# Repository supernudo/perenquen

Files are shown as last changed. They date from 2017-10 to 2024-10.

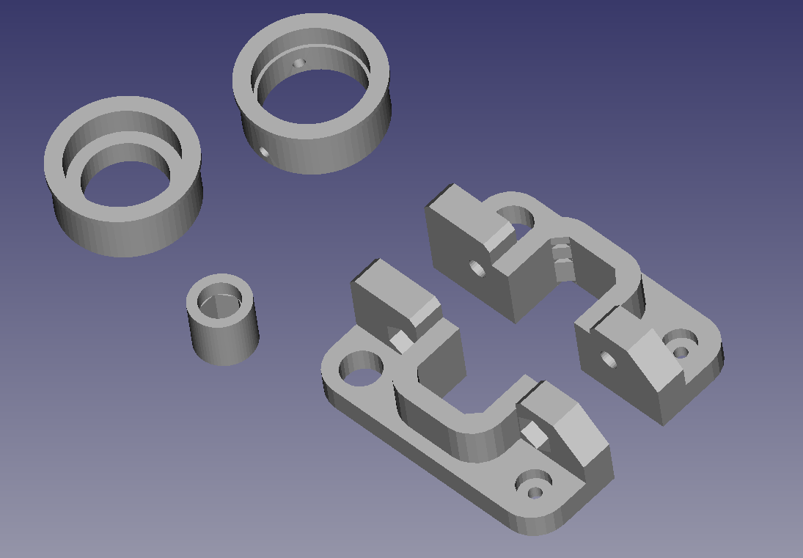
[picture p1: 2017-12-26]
Mechanics/manufacture/Piezas 2017-10-27 18-39-10.png

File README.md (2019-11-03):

# Perenquen

Robot de laberinto o micromouse.

Perenquén es mi primer robot de laberinto. Tiene una tracción diferencial de 4 ruedas diseñada para acelerar en recta a 10m/s/s y alcanza una velocidad de 3m/s. La posición de su centro de masa le permite hacer giros precisos sobre sus ruedas delanteras sin derrapar, a pesar de tener 4 ruedas. Para controlar su velocidad y posición utiliza encoders magnéticos. Durante las curvas utiliza un giroscopo para girar con precisión, independientemente de si derrapan las ruedas. Además, utiliza 4 sensores infrarrojos (2 delanteros y 2 diagonales) para navegar por el laberinto.

## Autor

Javier Baliñas Santos

## Licencia

Todos estos productos están liberados mediante [Creative Commons Attribution-ShareAlike 4.0 International License](http://creativecommons.org/licenses/by-sa/4.0/).  
*All these products are released under [Creative Commons Attribution-ShareAlike 4.0 International License](http://creativecommons.org/licenses/by-sa/4.0/).*

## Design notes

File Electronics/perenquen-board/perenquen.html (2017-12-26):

# Perenquen BOM Rev

Date

Company

# Balitronics

Comment 1

Comment 2

Comment 3

Comment 4

Total Parts

# 97 (Unique 49)

Ref

Qty

Value

Footprint

MPN

[C] -

C2 C9 C8

3

220u 10V

2917(imp) 7343(metric)

T491D227K010AT

C3 C11 C10 C23 C20 C21 C17 C18 C22 C15 C16

11

100n

Capacitors_SMD:C_0603

0603YC104KAT2A

C6

1

10u

Capacitors_SMD:C_0603

T491C106M016AT

C12 C1 C13 C4 C14

5

1u

Capacitors_SMD:C_0603

08053G105ZAT2A

C7

1

10n

Capacitors_SMD:C_0603

06035C103KAT2A

C5

1

470n

Capacitors_SMD:C_0603

0603YD474KAT2A

C19

1

10u 6V LowESR

2312(imp), 6032(metric)

T491C106M016AT

[D] -

D2

1

PWR-ON

0603

SML-D12V1WT86

D6

1

TX-L

LEDs:LED_D5.0mm

SFH4545

D7 D8

2

TX-LD

LEDs:LED_D5.0mm

SFH4545

D9

1

TX-R

LEDs:LED_D5.0mm

SFH4545

D1

1

LED1

0603

SML-D12P8WT86

D3

1

LED2

0603

SML-D12P8WT86

D4

1

LED3

0603

SML-D12P8WT86

D5

1

LED4

0603

SML-D12P8WT86

[J] -

J4

1

MOTOR-R

perenquen motor block

J6 J7

2

ENC-L

perenquen motor block

J1

1

PWR1

B3B-PH-K-S(LF)(SN)

J3

1

MOTOR-L

perenquen motor block

PREC010SAAN-RC

J8 J9

2

ENC-L

pin header 1x4 angled

PREC020SBAN-M71RC

J2

1

ICD

pin header 1x5 angled

PREC020SBAN-M71RC

J5

1

BT

socket strip 1x6 angled

801-87-006-20-001101

[Q] -

Q3

1

RX-L

TEFT4300

Q4

1

RX-R

TEFT4300

Q1 Q2

2

RX-LD

TEFT4300

Q5

1

FLASH

TEFT4300

[R] -

R24 R29 R22 R23 R30

5

1k8 1%

RC0603FR-071K8L

R6 R13 R12

3

0R

RC0805JR-070RL

R5 R8 R4 R7

4

47k

RC0603JR-0747KL

R25 R28

2

12R 1%

RC0805FR-0712RL

R26 R27

2

5.6R 1%

RMCF0805FT5R60

R10 R20

2

10k 1%

RC0603FR-0710KL

R1

1

2R2 1%

RC0603FR-072R2L

R9 R3 R2 R11 R14

5

10k

RC0603FR-0710KL

R15 R17 R18 R21 R16

5

1k

RC0603JR-071KL

R19

1

20k 1%

RC0603FR-0720KL

[SW] -

SW2 SW3 SW4

3

RST

B3U-1000P

SW1

1

450301014042

450301014042

[TP] -

TP1 TP3

2

MagINCn

TP2 TP4

2

MagDECn

[U] -

U2

1

M2940IMPX-5.0/NOPB

TO_SOT_Packages_SMD:SOT-223-3_TabPin2

M2940IMPX-5.0/NOPB

U11

1

DSPIC33EP512MC806

Housings_QFP:TQFP-64_10x10mm_Pitch0.5mm

DSPIC33EP512MC806-I/PT

U8 U7

2

ZXMHC3A01T8

Housings_SOIC:Zetex_SM8

ZXMHC3A01T8

U12

1

ULN2003A

ULN2003A

U6 U1

2

MCP1700

TO_SOT_Packages_SMD:SOT-23

MCP1700T-3302E/TT

U9 U10

2

AS5045B

Housings_SSOP:SSOP-16_5.3x6.2mm_Pitch0.65mm

AS5045B

U4 U3

2

TC4427COA

TC4427COA

U5

1

LY3200ALH

LY3200ALHTR

[Y] -

Y1

1

10Mhz

CSTCE10M0G55-R0

# BOM made with KICAD_BOM_WIZARD (https://github.com/HashDefineElectronics/KiCad_BOM_Wizard) (Generated mar 31 oct 2017 20:18:06 CET)

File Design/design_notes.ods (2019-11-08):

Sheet: motores
 |  | Min7 | Micromouse | Micromouse | Minisumo | Units
Maximum acceration and speed
Robot mass | m | 0,09 | 0,12 | 0,08 | 0,5 | kg | 44,5
Friction coheficient | u | 0,7 | 0,7 | 0,7 | 0,7
Gravity acceleration | g | 9,8 | 9,8 | 9,8 | 9,8 | m/s²
Max. Acceleration | a_max = g * k | 7,00 | 7,00 | 7,00 | 7,00 | m/s²
Max. Speed | v_max | 3,5 | 3 | 3 | 3 | m/s
Maximum power requiered
Force | F_max = m * a | 0,63 | 0,84 | 0,56 | 3,50 | N
Power | P_max = F * v | 2,21 | 2,52 | 1,68 | 10,50 | W
Power per motor | P_motor = P_max/2 | 1,10 | 1,26 | 0,84 | 5,25 | W
Min motor power | P_motor_min = 1.5 * P_motor | 1,65 | 1,89 | 1,26 | 7,88 | W
Max motor power | P_motor_max = 2 * P_motor | 2,21 | 2,52 | 1,68 | 10,50 | W
Gear ratio
Tires diameter | d_wheel | 24,00E-03 | 24,00E-03 | 24,00E-03 | 24,00E-03 | m
Torque requiered | M = F * radious | 7,56E-03 | 10,08E-03 | 6,72E-03 | 42,00E-03 | Nm
Torque per motor | M_motor = M/2 | 3,78E-03 | 5,04E-03 | 3,36E-03 | 2,10E-02 | Nm
Wheel circunference | l_wheel = pi*d_wheel | 7,54E-02 | 7,54E-02 | 7,54E-02 | 7,54E-02 | m
Motor angular speed | w_motor = v_max/l_wheel * 60[s/min] | 2785 | 2387 | 2387 | 2387 | rpm
 |  | 40 | 40 | 10
 |  | 12 | 12 | 1
 | K | 1,00 | 3,33 | 10,00 | 1
 | M_motor ‘ = M_motor/K | 3,78E-03 | 1,51E-03 | 3,36E-04 | 21,00E-03
 | w_motor’ = w_motor*k | 2785 | 7958 | 23873 | 2387
 | PN | 1717T006SR | 1524SR | HPCB 6V | 1524SR
 | U | 7,4 | 11,1 | 7,4 | 14,8 | V
 | R | 4,3 | 10,6 | 3,75 | 10,6 | Ohms
 | I0 | 0,046 | 0,009 | 0,12 | 0,009 | A
 | KE | 0,414 | 0,895 | 0,185 | 0,895 | mV/min^-1 |  | 0,014123103666667
 | KM | 3,96 | 8,55 | 1,91 | 8,55 | mNm/A
 | P2nom = R/4 * (U/R – I0)² | 3,02 | 2,856 | 3,220 | 5,10 | W
 | n0 = (U – (I0*R))/KE * 1000 | 17397 | 12296 | 37568 | 16430 | Min^-1
 | IH = U/R | 1,72 | 1,05 | 1,97
 | MH = KM * (IH-I0) | 6,63 | 8,88 | 3,54
 | n > n0/2 | FALSO | VERDADERO | VERDADERO | FALSO
 | M < MH/2 | FALSO | VERDADERO | VERDADERO | FALSO
 | P_motor_min > P2nom | VERDADERO | VERDADERO | VERDADERO | FALSO
 |  |  |  |  |  | 30000
 | m_motor | 36 | 36 | 19 |  | 0,18500000
 | m_bat | 8,5 | 12,45 | 12,45
 | d_pcb | 0,34 | 0,34 | 0,34 |  | 2,82462073333332
 | len | 10 | 10 | 10 |  | 1,52407593525179
 | width | 7,5 | 7,5 | 7,5 |  | 0,454657917717437
 | m_pcb | 26 | 26 | 26
 | m_others | 2 | 2 | 2 | 1,90852752252251
 | m_total | 90 | 94 | 77

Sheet: motores_hp
 |  | Robot example | Perenquén | Pumatrón 10:1 | Pumatrón 5:1 | Units
Acceleration and speed requierements
Robot mass | m | 0,1 | 0,11 | 0,07 | 0,07 | kg
Friction coheficient | u | 0,9 | 0,7 | 0,9 | 0,9
Gravity acceleration | g | 9,8 | 9,8 | 9,8 | 9,8 | m/s²
Max. Acceleration | a_max = g * u | 8,82 | 6,86 | 8,82 | 8,82 | m/s²
Max. Speed | v_max | 3 | 4,25 | 4,25 | 6 | m/s
Motor power requierements
Force | F_max = m * a | 0,88 | 0,75 | 0,62 | 0,62 | N
Power | P_max = F * v | 2,65 | 3,21 | 2,62 | 3,70 | w
Power per motor | P_motor = P_max / 2 | 1,32 | 1,60 | 1,31 | 1,85 | w
Min motor power | P_motor_min = 1.5 * P_motor | 1,98 | 2,41 | 1,97 | 2,78 | w
Max motor power | P_motor_max = 2 * P_motor | 2,65 | 3,21 | 2,62 | 3,70 | w
Motor torque and speed requierements
Wheel diameter | d_wheel | 24,00E-03 | 24,00E-03 | 24,00E-03 | 24,00E-03 | m
Wheel circunference | l_wheel = PI * d_wheel | 7,54E-02 | 7,54E-02 | 7,54E-02 | 7,54E-02 | m
Total torque requiered | M = F * d_wheel / 2 | 10,58E-03 | 9,06E-03 | 7,41E-03 | 7,41E-03 | Nm
Torque per wheel | M_wheel = M / 2 | 5,29E-03 | 4,53E-03 | 3,70E-03 | 3,70E-03 | Nm
Wheel angular speed | w_wheel = v_max / l_wheel * 60[s/min] | 2387 | 3382 | 3382 | 4775 | Min^-1
Gear ratio | KG | 10,000 | 10,000 | 10,000 | 5,000
Motor torque | M_motor = M_wheel / KG | 5,29E-04 | 4,53E-04 | 3,70E-04 | 7,41E-04 | Nm
Min motor torque | M_motor_min = 1.5 * M_motor | 7,94E-04 | 6,79E-04 | 5,56E-04 | 1,11E-03 | Nm
Max motor torque | M_motor_max = 2 * M_motor | 1,59E-03 | 1,36E-03 | 1,11E-03 | 2,22E-03 | Nm
Motor speed | w_motor’ = w_wheel * KG | 23873 | 33820 | 33820 | 23873 | Min^-1
Motor + gear assembly nominal parameters |  | HPCB 6V | HPCB 6V | HPCB 6V | HPCB 6V
Gear ratio | KG | 4,995 | 4,995 | 4,995 | 4,995
Nominal voltage | Un | 6 | 6 | 6 | 6 | V
Free-run speed after KG @Un | n0_out | 6000 | 6000 | 6000 | 6000 | Min^-1
Free-run current @Un | I0 | 0,12 | 0,12 | 0,12 | 0,12 | A
Stall current @Un | IH | 1,6 | 1,6 | 1,6 | 1,6 | A
Stall torque after KG @Un | MH_out | 14,12 | 14,12 | 14,12 | 14,12 | mNm
Motor nominal parameters
Free-run speed before KG @Un | n0 = n0_out*KG | 29970 | 29970 | 29970 | 29970 | Min^-1
Resistance | R = Un/IH | 3,75 | 3,75 | 3,75 | 3,75 | Ohms
Stall torque before KG @Un | MH = MH_out/KG | 2,827 | 2,827 | 2,827 | 2,827 | mNm
Electrical constant | KE = (Un – (I0*R))/n0 * 1000 | 0,185 | 0,185 | 0,185 | 0,185 | mV/min^-1
Mechanical constant | KM = MH/(IH-I0) | 1,91 | 1,91 | 1,91 | 1,91 | mNm/A
Power | P2nom = R/4 * (U/R – I0)² | 2,054 | 2,054 | 2,054 | 2,054 | w
Motor application parameters
Voltage | U | 6,000 | 7,000 | 7,000 | 7,000 | V
Free-run speed | n0 = (U – (I0*R))/KE * 1000 | 29970 | 35370 | 35370 | 35370 | Min^-1
Stall current | IH = U/R | 1,600 | 1,867 | 1,867 | 1,867 | A
Stall torque | MH = KM * (IH-I0) | 2,827 | 3,337 | 3,337 | 3,337 | mNm
Power | P2nom = R/4 * (U/R – I0)² | 2,054 | 2,860 | 2,860 | 2,860 | w
Design rules
Speed condition with gearbox | n > n0 / 2 | VERDADERO | VERDADERO | VERDADERO | VERDADERO
 | n < n0 | VERDADERO | VERDADERO | VERDADERO | VERDADERO
Power condition with gearbox | M < MH / 2 | VERDADERO | VERDADERO | VERDADERO | VERDADERO
Maximun power condition | P_motor_min > P2nom | VERDADERO | VERDADERO | VERDADERO | VERDADERO

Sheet: telemetria
Velocidad | 1382400 | bits/s
 | 138240 | bytes/s
 | 138,24 | bytes/ms
UART interrupt | 0,0072 | ms | 3,7
Ts | 1 | ms
Tasa | 138,24 | bytes/Ts | 34,56
 | 69,12 | int16_t/Ts
Datos | 20 | bytes
Datos ASCII | 160 | bytes
Datos en 1s | 0,043402777777778
 | BRGH=0 | BRGH=1
Fp | 60000000
Baudrate | 921600
UxBRG | 3,069 | 15,276
UxBRG' | 3,000 | 15,000
Baudrate' | 937500,00 | 937500,00
Error | 1,73 | 1,73
Fin | 10000000
Fcy | 60000000
Fosc | 120000000
N1 | 2
N2 | 2
M | 48 | 48
Fvco | 240000000
Fpllo | 120000000
 | 60000000
BT 2.0 + EDR | 2100000 | bits/s
 | 262500 | bytes/s
 | 262,5 | bytes/ms

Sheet: cs
Velocidad max. | 3 | m/s
 | 0,003 | m/ms
 | 3 | mm/ms
Ts | 1 | ms
Distancia/Ts | 3 | mm
 | 153,387916918683 | pulsos
Diametro rueda | 25,50 | mm
Longitud/vuelta | 80,11 | mm
Pulsos por vuelta | 4096,00 | pulsos
Ratio pulsos/mm | 51,13 | pulsos/mm
Pulsos/Ts

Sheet: dinamica
Estudio del fenomeno de derrape en fase de aceleracion
P1(kg) | 1,000 | Peso robot sobre el eje motriz
P2(kg) | 1,000 | Peso de cubo al límite de agarre
Ka | 1,000 | Coeficiente de aderencia
g(m/s2) | 9,800 | Constante de gravedad
d1(m) | 0,0000 | Distancia del eje motriz al centro de masas
d2(m) | 0,1500 | Distancia del centro de masas al eje de apoyo
d(m) | 0,1500 | Distancia entre eje motriz y eje de apoyo
z(m) | 0,1120 | Altura del centro de masas
d3 | 15,0000 | Distancia al centro de masas desde la cara derecha del robot
Para un robot simetrico:
 |  |  |  | 0,01
Aceleracion/Frenado:
a_max(g) | 0,573 | Aceleracion máxima para no derrapar/caballito
a_max(m/s2) | 5,611 | Aceleracion máxima para no derrapar/caballito
Eleccion del perfil de velocidad
a_max(m/s2) | 5,611 | Aceleracion máxima
a(m/s2) | 4,489 | Aceleracion de seguridad
d(m) | 1,000 | Desplazamiento
v_max(m/s) | 1,000 | Velocidad máxima
t1, t3(s) | 0,223 | Duración de la fase de aceleración y frenado
d1, d3(m) | 0,111 | Distancia recorrida en fase de aceleracion y frenado
d2(m) | 0,777 | Distancia recorrida en fase de velocidad cte
t2(s) | 0,777 | Duranción de la fase de velocidad cte
t(s) | 1,223 | Duración del desplazamiento total
Cambio de sistema de unidades SI/robot
Valores en unidades SI:
d(m) | 1,000000 | Distancia lineal
v(m/s) | 3,000 | Velocidad lineal
a(m/s2) | 10,000 | Aceleracion lineal
alpha(grados) | 360,000 | Angulo
Variables dependientes:
Ts(s) | 0,001 | Periodo de muestreo
N(pulsos/vuelta) | 1024,000 | Numero de pulsos del encoder
Mult_N | 4,000 | Factor de multiplicacion de pulsos de encoder
D_enc(m) | 0,0255 | Diametro rueda del encoder
d_track(m) | 0,0670 | Distancia entre encoders
K(pulsos/m) | 51129,186 | Constante de conversion lineal SI/robot
K_mult | 10,000 | Factor de multiplicacion de K para poder trabajar con aceleraciones enteras
Constantes conversion:
coef_d(pulsos/m) | 511291,861 | Coeficiente de conversion de distancia
coef_v((pulsos/Ts)/(m/s)) | 511,292 | Coeficiente de conversion de velocidad
coef_a((pulsos/Ts2)/(m/s2)) | 0,511 | Coeficiente de conversión de aceleracion
coef_alpha(pulsos/grado) | 2989,455 | Coeficiente de conversion de angulo
Valores en unidades robot:
d_robot(pulsos) | 511291,861 | Distancia lineal
v_robot(pulsos/Ts) | 1533,876 | Velocidad lineal
a_robot(d(pulsos/Ts)) | 5,113 | Aceleracion lineal
angle_robot(pulsos) | 1076203,922 | Angulo
Calibración de d_track
angle_consign | 3600,000 |  | 7200
angle_measured | 3580,703 |  | 7240,255
gain_error | 1,00538907 |  | 0,994440099107817
a (sin) | 6,150 | 6,150 | 11,6
b (cos) | 16,800 |  | 13,7000000000
c (hypo) | 17,800 |  | 17,9513230710162
alpha_atang(grados) | 20,106 |  | 40,255
alpha_cos(grados) | 19,297 |  | 40,255
alpha_sen(grados) | 20,213 |  | 40,255
d_track_nom(m) | 292,00000000000 | Distancia entre encoders nominal | 292,00000000000
d_track_calib(m) | 293,57360825271 | Distancia entre encoders calibrada | 290,37650893948
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

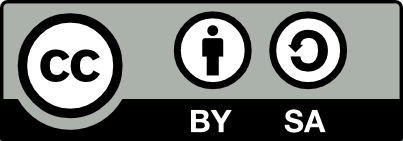
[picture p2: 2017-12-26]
Electronics/perenquen-board/attribution-share-alike-creative-commons-license.png

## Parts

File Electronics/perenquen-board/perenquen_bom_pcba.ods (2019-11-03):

Title | Perenquen
Revision | OSHWDem17
Date | 2017-11-01
Generated | jue 09 nov 2017 10:52:51 CET
Company | Balitronics
Comment 1 | Author: Javier Baliñas Santos
Comment 2
Comment 3
Comment 4
Total Parts | 90
Total Unique Parts | 49
Ref | Qty | Value | Footprint | MPN
C12 C1 C13 C4 C14 | 5 | 1u | Capacitors_SMD:C_0805 | 08053G105ZAT2A
C19 | 1 | 10u 6V LowESR | Capacitors_Tantalum_SMD:CP_Tantalum_Case-U_EIA-6032-15_Reflow | T491C106M016AT
C2 C9 C8 | 3 | 220u 10V | Capacitors_Tantalum_SMD:CP_Tantalum_Case-X_EIA-7343-43_Reflow | T491D227K010AT
C3 C11 C10 C23 C20 C21 C17 C18 C22 C15 C16 | 11 | 100n | Capacitors_SMD:C_0603 | 0603YC104KAT2A
C5 | 1 | 470n | Capacitors_SMD:C_0603 | 0603YD474KAT2A
C6 | 1 | 10u | Capacitors_SMD:C_0603 | T491C106M016AT
C7 | 1 | 10n | Capacitors_SMD:C_0603 | 06035C103KAT2A
D1 | 1 | LED1 | Diodes_SMD:D_0603 | SML-D12P8WT86
D2 | 1 | PWR-ON | Diodes_SMD:D_0603 | SML-D12V1WT86
D3 | 1 | LED2 | Diodes_SMD:D_0603 | SML-D12P8WT86
D4 | 1 | LED3 | Diodes_SMD:D_0603 | SML-D12P8WT86
D5 | 1 | LED4 | Diodes_SMD:D_0603 | SML-D12P8WT86
D6 | 1 | TX-L | LEDs:LED_D5.0mm_Horizontal_O1.27mm_Z3.0mm | SFH4545
D7 | 1 | TX-RD | LEDs:LED_D5.0mm_Horizontal_O1.27mm_Z3.0mm | SFH4545
D8 | 1 | TX-LD | LEDs:LED_D5.0mm_Horizontal_O1.27mm_Z3.0mm | SFH4545
D9 | 1 | TX-R | LEDs:LED_D5.0mm_Horizontal_O1.27mm_Z3.0mm | SFH4545
J1 | 1 | PWR1 | Connectors_JST:JST_PH_B3B-PH-K_03x2.00mm_Straight | B3B-PH-K-S(LF)(SN)
J2 | 1 | ICD | Pin_Headers:Pin_Header_Angled_1x05_Pitch2.54mm | 68016-410HLF
J3 | 1 | BT | Socket_Strips:Socket_Strip_Straight_1x06_Pitch2.54mm | 801-87-006-20-001101
J4 | 1 | ENC-L | Pin_Headers:Pin_Header_Angled_1x04_Pitch2.54mm | 68016-410HLF
J5 | 1 | ENC-R | Pin_Headers:Pin_Header_Angled_1x04_Pitch2.54mm | 68016-410HLF
M1 | 1 | Motor-block | balitronics_kicad_footprint_lib:Perenquen-motor-block
Q1 Q2 | 2 | RX-LD | LEDs:LED_D3.0mm_Horizontal_O1.27mm_Z2.0mm | TEFT4300
Q3 | 1 | RX-L | LEDs:LED_D3.0mm_Horizontal_O1.27mm_Z2.0mm | TEFT4300
Q4 | 1 | RX-R | LEDs:LED_D3.0mm_Horizontal_O1.27mm_Z2.0mm | TEFT4300
Q5 | 1 | FLASH | LEDs:LED_D3.0mm | TEFT4300
R1 | 1 | 2R2 1% | Resistors_SMD:R_0603 | RC0603FR-072R2L
R10 R20 | 2 | 10k 1% | Resistors_SMD:R_0603 | RC0603FR-0710KL
R15 R17 R18 R21 R16 | 5 | 1k | Resistors_SMD:R_0603 | RC0603JR-071KL
R19 | 1 | 20k 1% | Resistors_SMD:R_0603 | RC0603FR-0720KL
R24 R29 R22 R23 R30 | 5 | 1k8 1% | Resistors_SMD:R_0603 | RC0603FR-071K8L
R25 R28 | 2 | 12R 1% | Resistors_SMD:R_0805 | RC0805FR-0712RL
R26 R27 | 2 | 5.6R 1% | Resistors_SMD:R_0805 | RMCF0805FT5R60
R5 R8 R4 R7 | 4 | 47k | Resistors_SMD:R_0603 | RC0603JR-0747KL
R6 R13 R12 | 3 | 0R | Resistors_SMD:R_0805 | RC0805JR-070RL
R9 R3 R2 R11 R14 | 5 | 10k | Resistors_SMD:R_0603 | RC0603FR-0710KL
SW1 | 1 | 450301014042 | Pin_Headers:Pin_Header_Straight_1x03_Pitch2.54mm | 450301014042
SW2 | 1 | RST | Buttons_Switches_SMD:SW_SPST_B3U-1000P | B3U-1000P
SW3 | 1 | USR1 | Buttons_Switches_SMD:SW_SPST_B3U-1000P | B3U-1000P
SW4 | 1 | USR2 | Buttons_Switches_SMD:SW_SPST_B3U-1000P | B3U-1000P
U11 | 1 | DSPIC33EP512MC806 | Housings_QFP:TQFP-64_10x10mm_Pitch0.5mm | DSPIC33EP512MC806-I/PT
U12 | 1 | ULN2003A | Housings_SSOP:SSOP-16_4.4x5.2mm_Pitch0.65mm | ULN2003APW
U2 | 1 | M2940IMPX-5.0 | TO_SOT_Packages_SMD:SOT-223-3_TabPin2 | LM2940IMPX-5.0/NOPB
U4 U3 | 2 | TC4427COA | SMD_Packages:SOIC-8-N | TC4427COA
U5 | 1 | LY3200ALH | balitronics_kicad_footprint_lib:Gyro_ST_LGA10 | LY3200ALHTR
U6 U1 | 2 | MCP1700 | TO_SOT_Packages_SMD:SOT-23 | MCP1700T-3302E/TT
U8 U7 | 2 | ZXMHC3A01T8 | Housings_SOIC:Zetex_SM8 | ZXMHC3A01T8TA
U9 U10 | 2 | AS5045B | Housings_SSOP:SSOP-16_5.3x6.2mm_Pitch0.65mm | AS5045B
Y1 | 1 | 10Mhz | balitronics_kicad_footprint_lib:Resonator_Murata_CSTCE_3pin | CSTCE10M0G55-R0
BOM made with KICAD_BOM_WIZARD (https://github.com/HashDefineElectronics/KiCad_BOM_Wizard.git)
Generated jue 09 nov 2017 10:52:51 CET

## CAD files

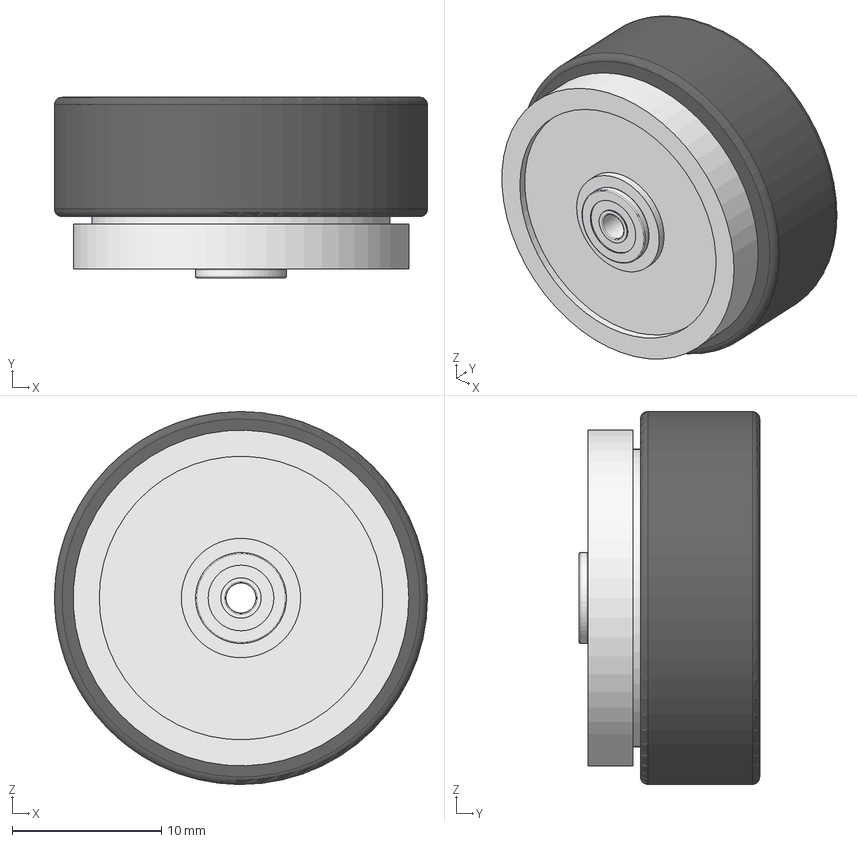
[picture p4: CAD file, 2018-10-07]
Mechanics/assemblies/wheel_front_assembly.fcstd
25.0 x 12.1 x 25.0 mm
miniz_wheel_8_5mm_01
ds0_5_45_01
C_SFL682ZZ_stp1_01
C_SFL682ZZ_stp1_01001
miniz_tire_8_5mm_01

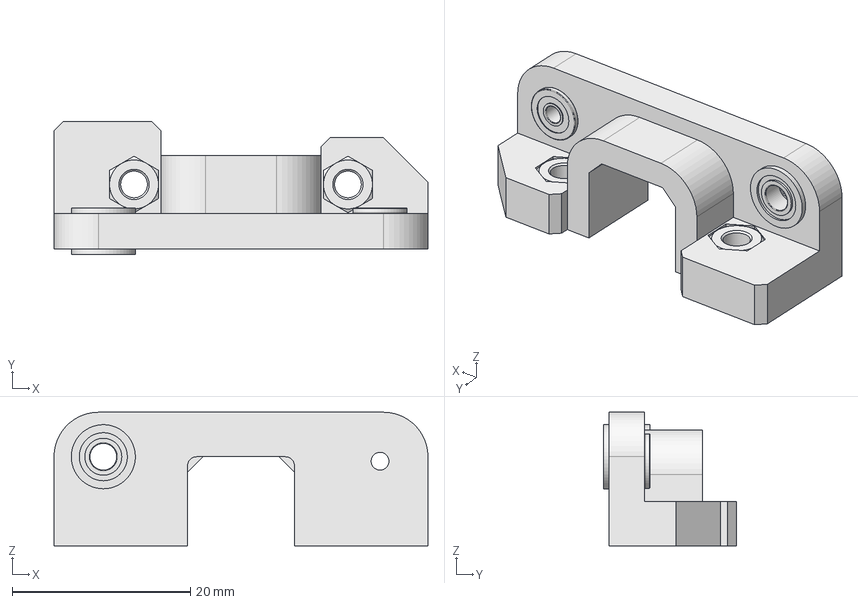
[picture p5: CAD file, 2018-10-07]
Mechanics/assemblies/main_support.fcstd
42.0 x 14.9 x 15.0 mm
gearbox_support_01
C_SFL682ZZ_stp1_01
FM63ZZ_01
FM63ZZ_02
ISO4032_Hex_Nut_M3_02
ISO4032_Hex_Nut_M3_03

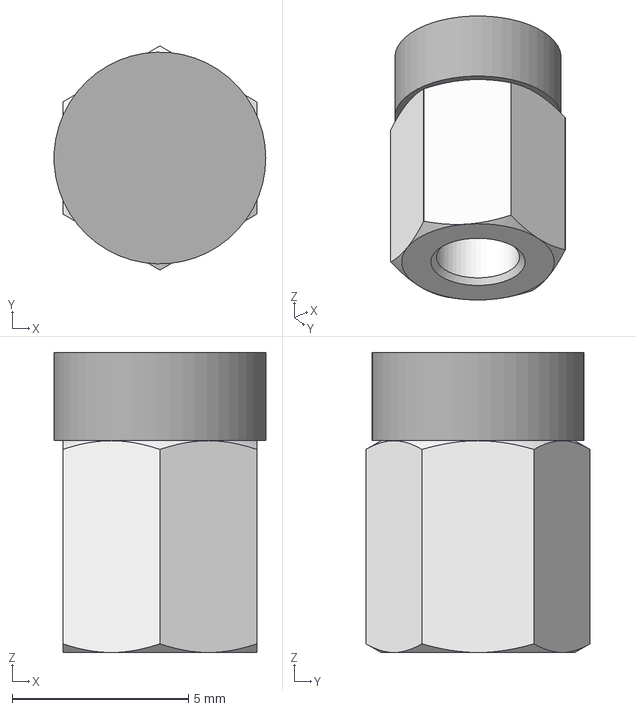
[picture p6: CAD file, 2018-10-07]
Mechanics/assemblies/magnent_assembly.fcstd
5.99 x 6.35 x 8.50 mm
ISO4032_Hex_Nut_M3_spacer_L6mm_01
AS5000_MD6H_1_01

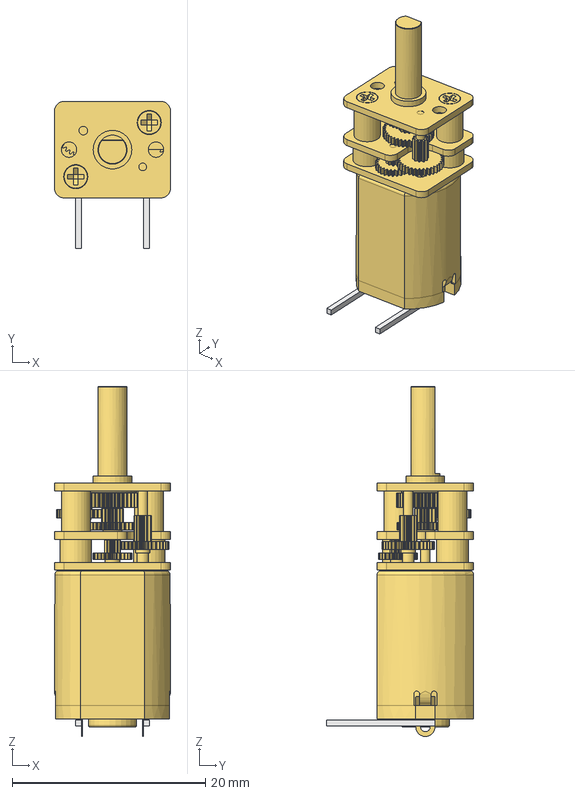
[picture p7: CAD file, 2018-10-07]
Mechanics/assemblies/mmgm-carbon-assembly.fcstd
12.0 x 15.3 x 36.2 mm
micro_metal_gearmotor_carbon_step1_01
pin_pcb_01
pin_pcb_01001

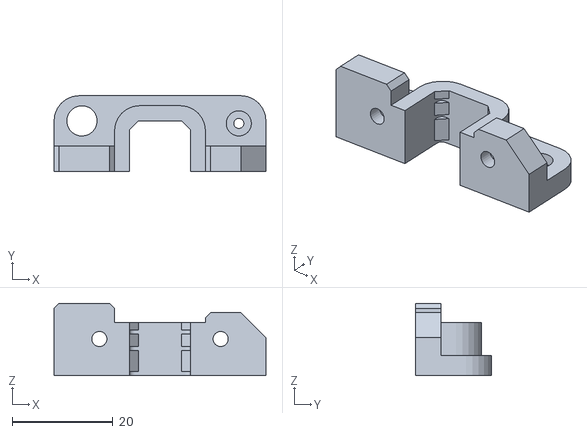
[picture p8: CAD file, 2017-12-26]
Mechanics/manufacture/main_support_left.stl
42.0 x 15.0 x 14.3

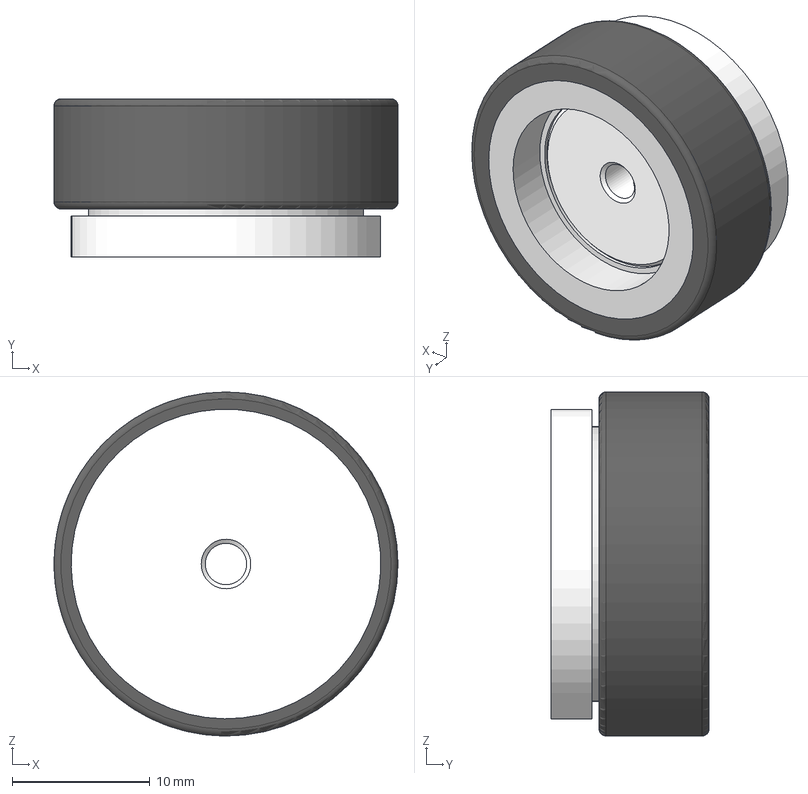
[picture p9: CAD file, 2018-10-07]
Mechanics/assemblies/wheel_rear_assembly.fcstd
25.0 x 11.5 x 25.0 mm
miniz_wheel_8_5mm_01
miniz_tire_8_5mm_01
S50D45Bas0303_01

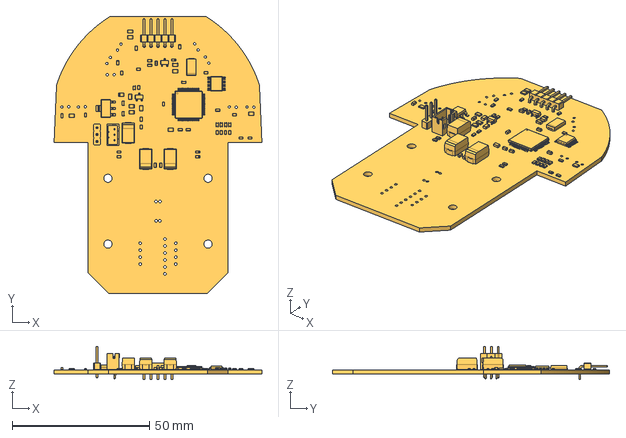
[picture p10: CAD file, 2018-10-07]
Mechanics/parts/mainboard.fcstd
75.8 x 101.0 x 12.2 mm

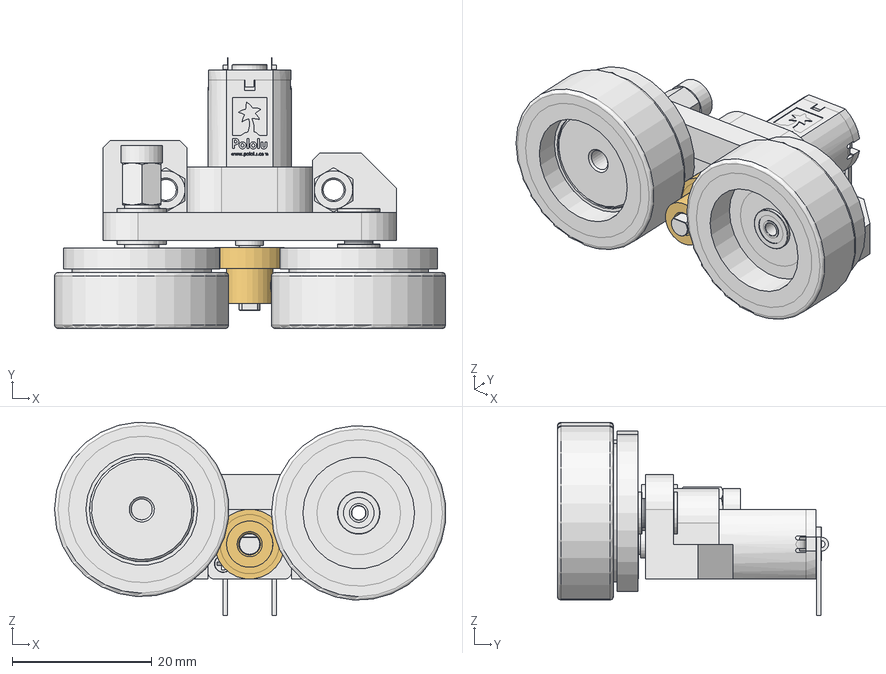
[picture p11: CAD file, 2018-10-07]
Mechanics/assemblies/motor_block_assembly.fcstd
56.0 x 38.8 x 27.7 mm
main_support_01
wheel_front_assembly_01
wheel_rear_assembly_01
s50b20b_0303_01
washer_2mm_01
washer_3mm_01
washer_2mm_02
washer_2mm_hacked_to_3mm_01
magnent_assembly_01
mmgm_carbon_assembly_01

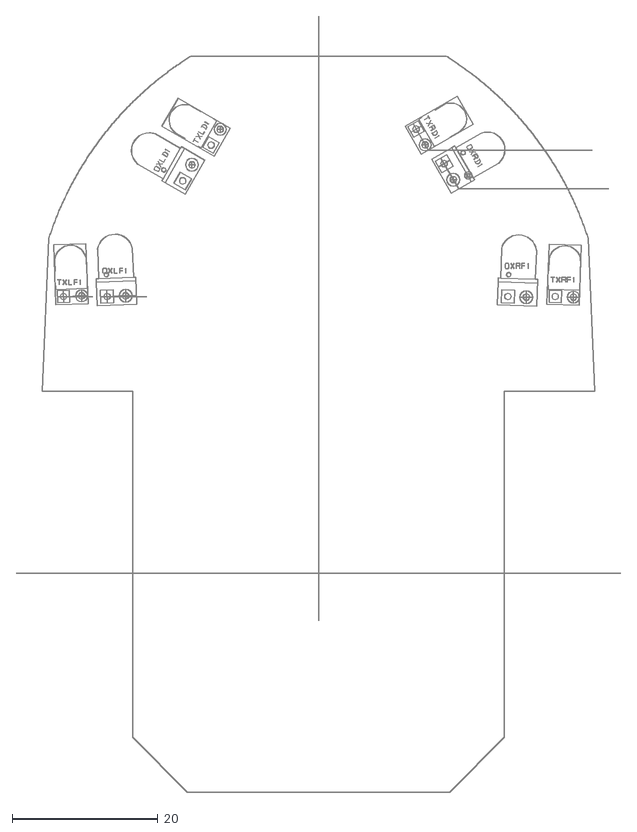
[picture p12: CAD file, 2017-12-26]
Electronics/perenquen-board/MIN7 PCB template.dxf
83.0 x 106.5

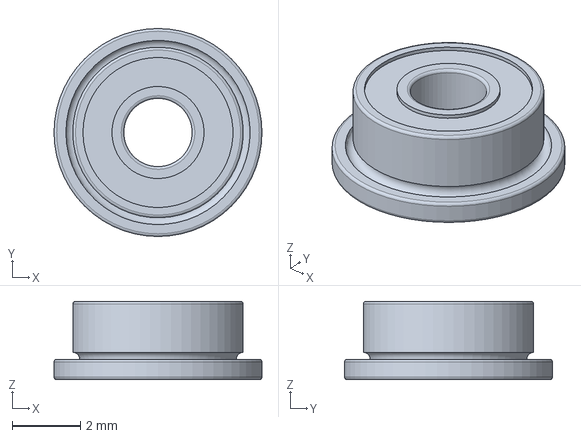
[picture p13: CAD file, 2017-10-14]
Mechanics/3th_party_parts/bearings/C-SFL682ZZ/C-SFL682ZZ.stp
6.10 x 6.10 x 2.30 mm

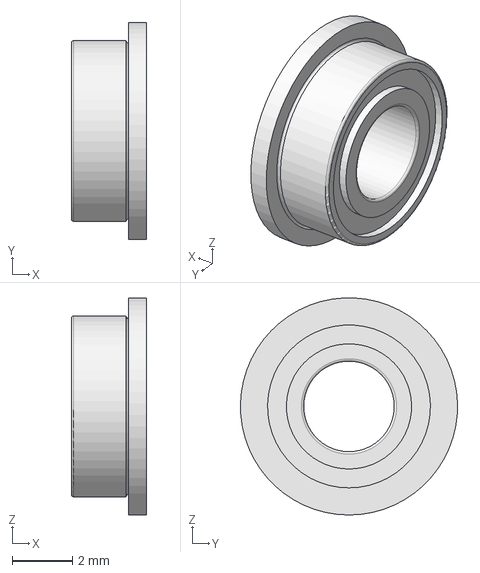
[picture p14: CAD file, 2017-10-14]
Mechanics/3th_party_parts/bearings/MF63ZZ/FM63ZZ.fcstd
2.50 x 7.20 x 7.19 mm

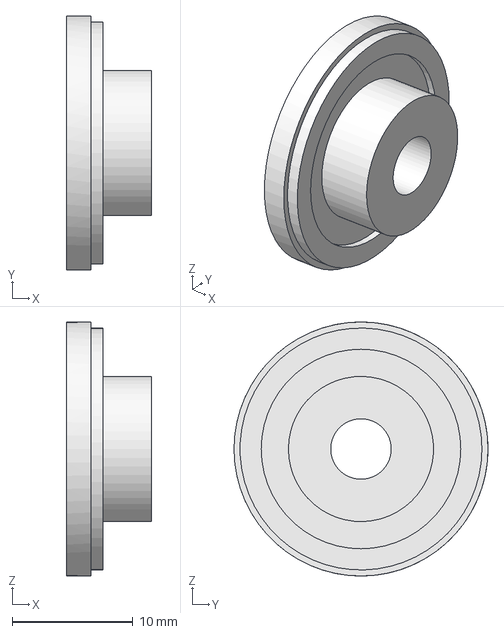
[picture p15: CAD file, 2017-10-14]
Mechanics/3th_party_parts/gears/ds0.5-40/ds0.5-40.fcstd
7.00 x 21.0 x 21.0 mm

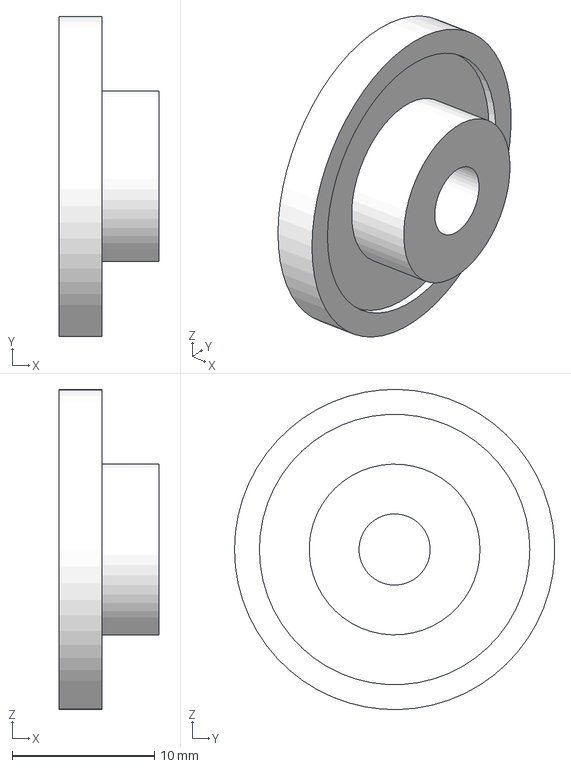
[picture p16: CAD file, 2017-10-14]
Mechanics/3th_party_parts/gears/ds0.5-45/ds0.5-45.fcstd
7.00 x 22.5 x 22.5 mm

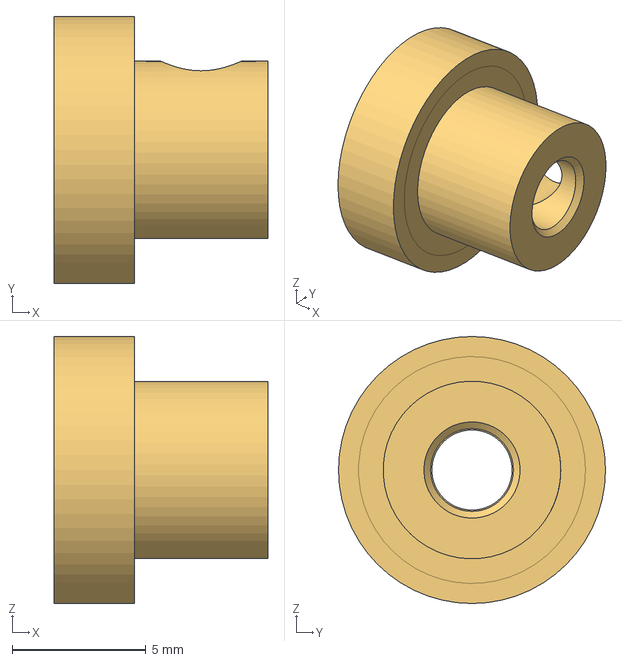
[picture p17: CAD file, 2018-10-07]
Mechanics/3th_party_parts/gears/s50b20b+0303/s50b20b+0303.fcstd
8.00 x 10.0 x 10.0 mm

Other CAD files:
Mechanics/manufacture/main_support_right.stl
Mechanics/3th_party_parts/gears/S50D45Bas0303/S50D45Bas0303.fcstd
Mechanics/3th_party_parts/magnents/AS5000_MD6H_1.fcstd
Mechanics/3th_party_parts/motors/hp_bracket_by_sinoptic/hp_bracket.fcstd
Mechanics/3th_party_parts/bearings/C-SFL682ZZ/F682ZZ.fcstd
Mechanics/3th_party_parts/bearings/C-SFL682ZZ/c-sfl682zz.dxf
Mechanics/3th_party_parts/bearings/MF63ZZ/FL673ZZ.stp
Mechanics/3th_party_parts/bearings/MF63ZZ/MF63ZZ.dxf
Mechanics/3th_party_parts/gears/S50D45Bas0303/S50D45Bas0303.dxf
Mechanics/3th_party_parts/gears/ds0.5-40/ds0.5-40.dxf
Mechanics/3th_party_parts/gears/ds0.5-45/ds0.5-45.dxf
Mechanics/3th_party_parts/gears/s50b20b+0303/s50b20b+0303.dxf
Mechanics/3th_party_parts/motors/hp_bracket_by_sinoptic/gearmotor_b1r.stl
Mechanics/3th_party_parts/motors/pololu/mmgm-carbon.fcstd
Mechanics/3th_party_parts/nuts/ISO4032_Hex_Nut_M3.fcstd
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

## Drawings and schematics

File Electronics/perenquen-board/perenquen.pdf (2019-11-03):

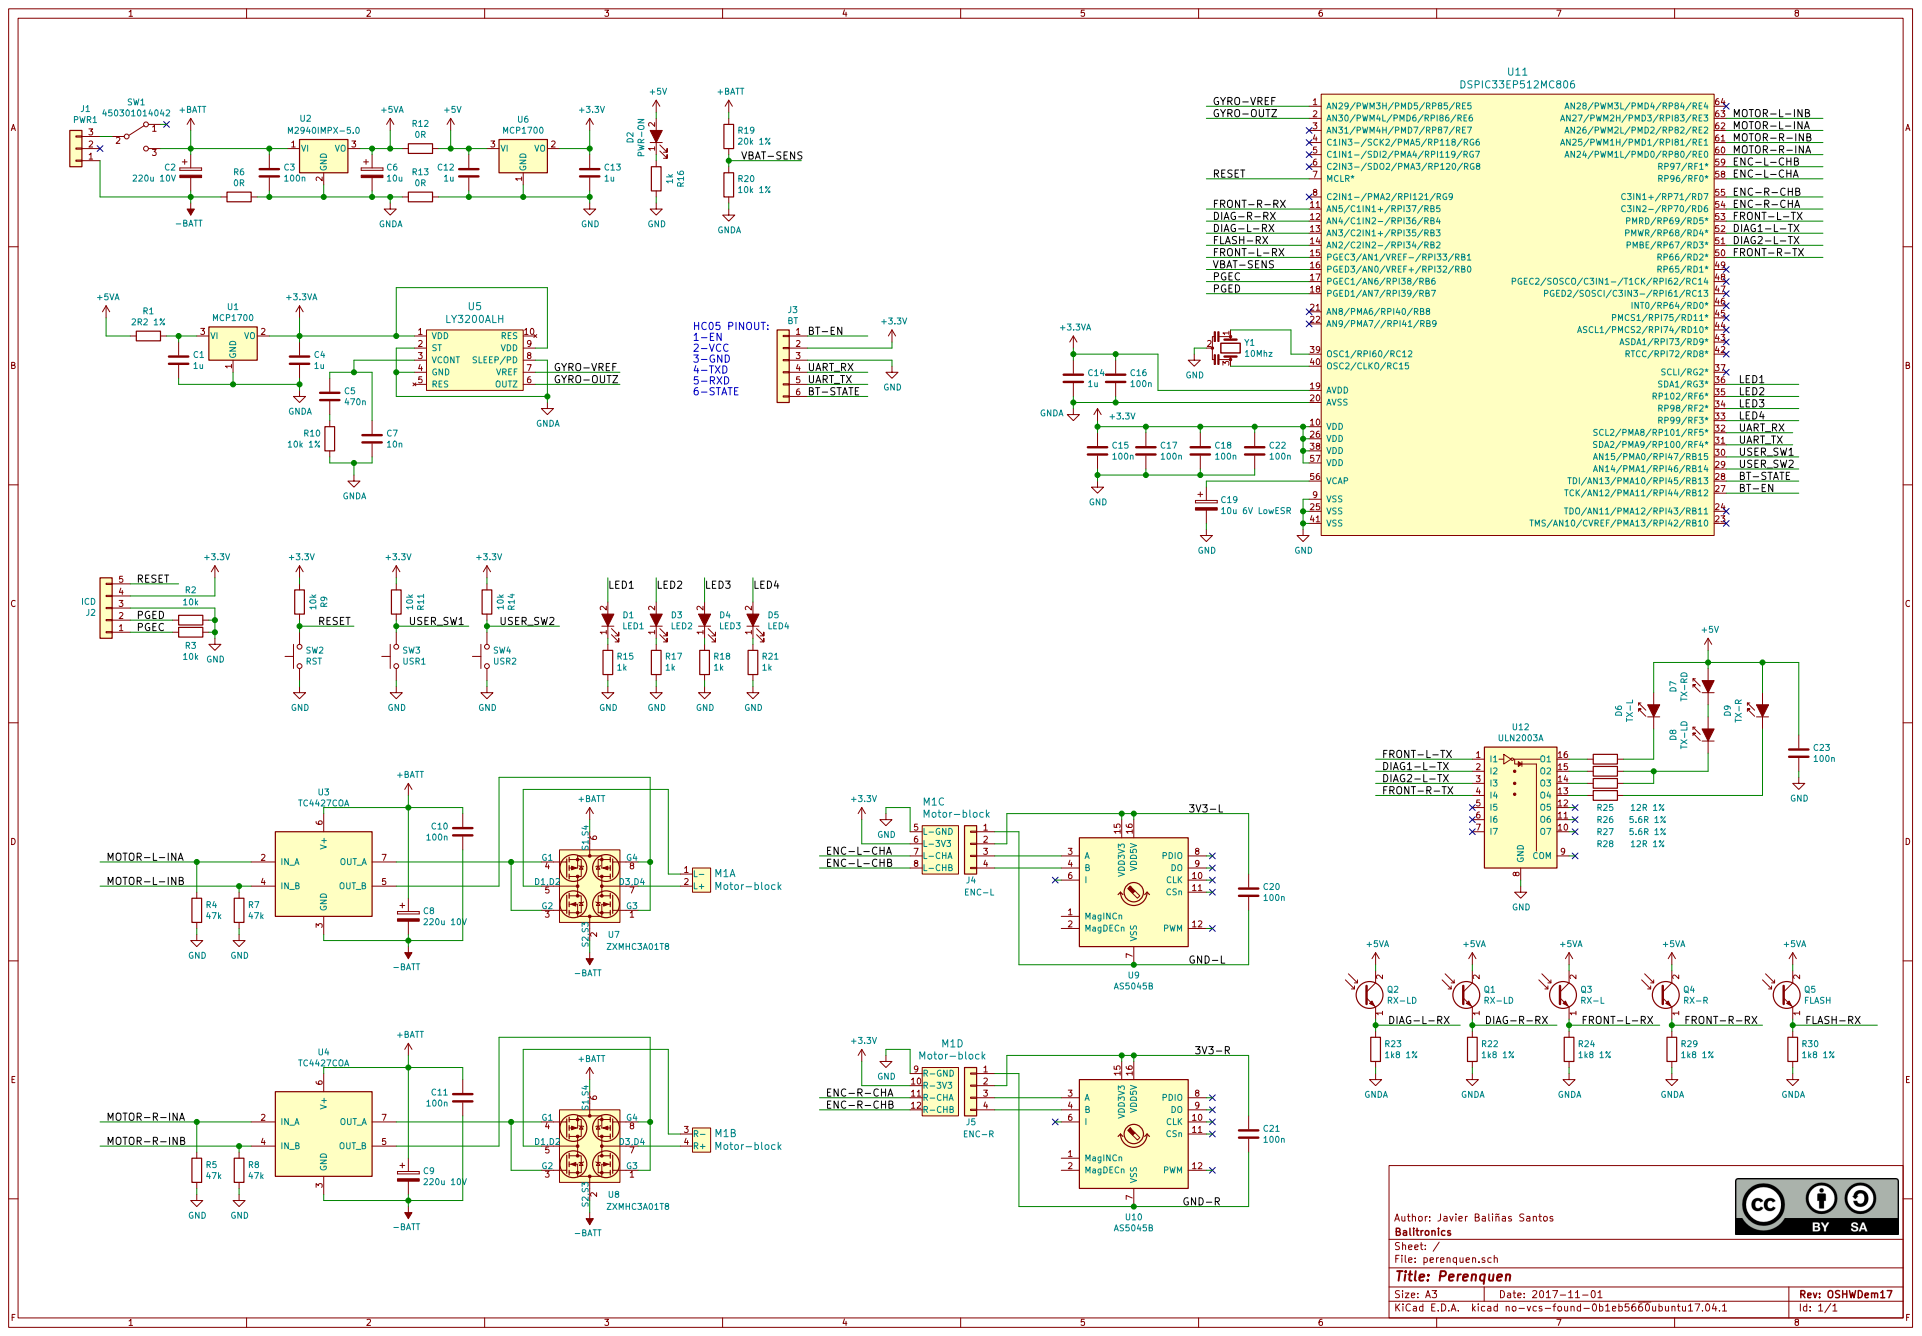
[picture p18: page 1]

2 VO 3 U2 M2940IMPX-5.0 AN29/PWM3H/PMD5/RP85/RE5 1 VDD 10 AN5/C1IN1+/RPI37/RB5 11 AN4/C1IN2-/RPI36/RB4 12 AN3/C2IN1+/RPI35/RB3 13 AN2/C2IN2-/RPI34/RB2 14 PGEC3/AN1/VREF-/RPI33/RB1 15 PGED3/AN0/VREF+/RPI32/RB0 16 PGEC1/AN6/RPI38/RB6 17 PGED1/AN7/RPI39/RB7 18 AVDD 19 AN30/PWM4L/PMD6/RPI86/RE6 2 AVSS 20 AN8/PMA6/RPI40/RB8 21 AN9/PMA7//RPI41/RB9 22 TMS/AN10/CVREF/PMA13/RPI42/RB10
+3.3V GNDA

FLASH-RX
FRONT-L-RX

1 VO 2 VI 3 U1 MCP1700 MagINCn 1 MagDECn 2 A

BT-STATE
BT-EN

I2 2
I3 3

FRONT-R-TX | I4 4

7 PDIO 8 DO 9 CLK 10 CSn 11 PWM 12 VDD3V3 15 VDD5V 16 U9 AS5045B R24

7 PDIO 8 DO 9 CLK 10 CSn 11 PWM 12 VDD3V3 15 VDD5V 16 U10 AS5045B

File: perenquen.sch Sheet: / Balitronics Author: Javier Baliñas Santos

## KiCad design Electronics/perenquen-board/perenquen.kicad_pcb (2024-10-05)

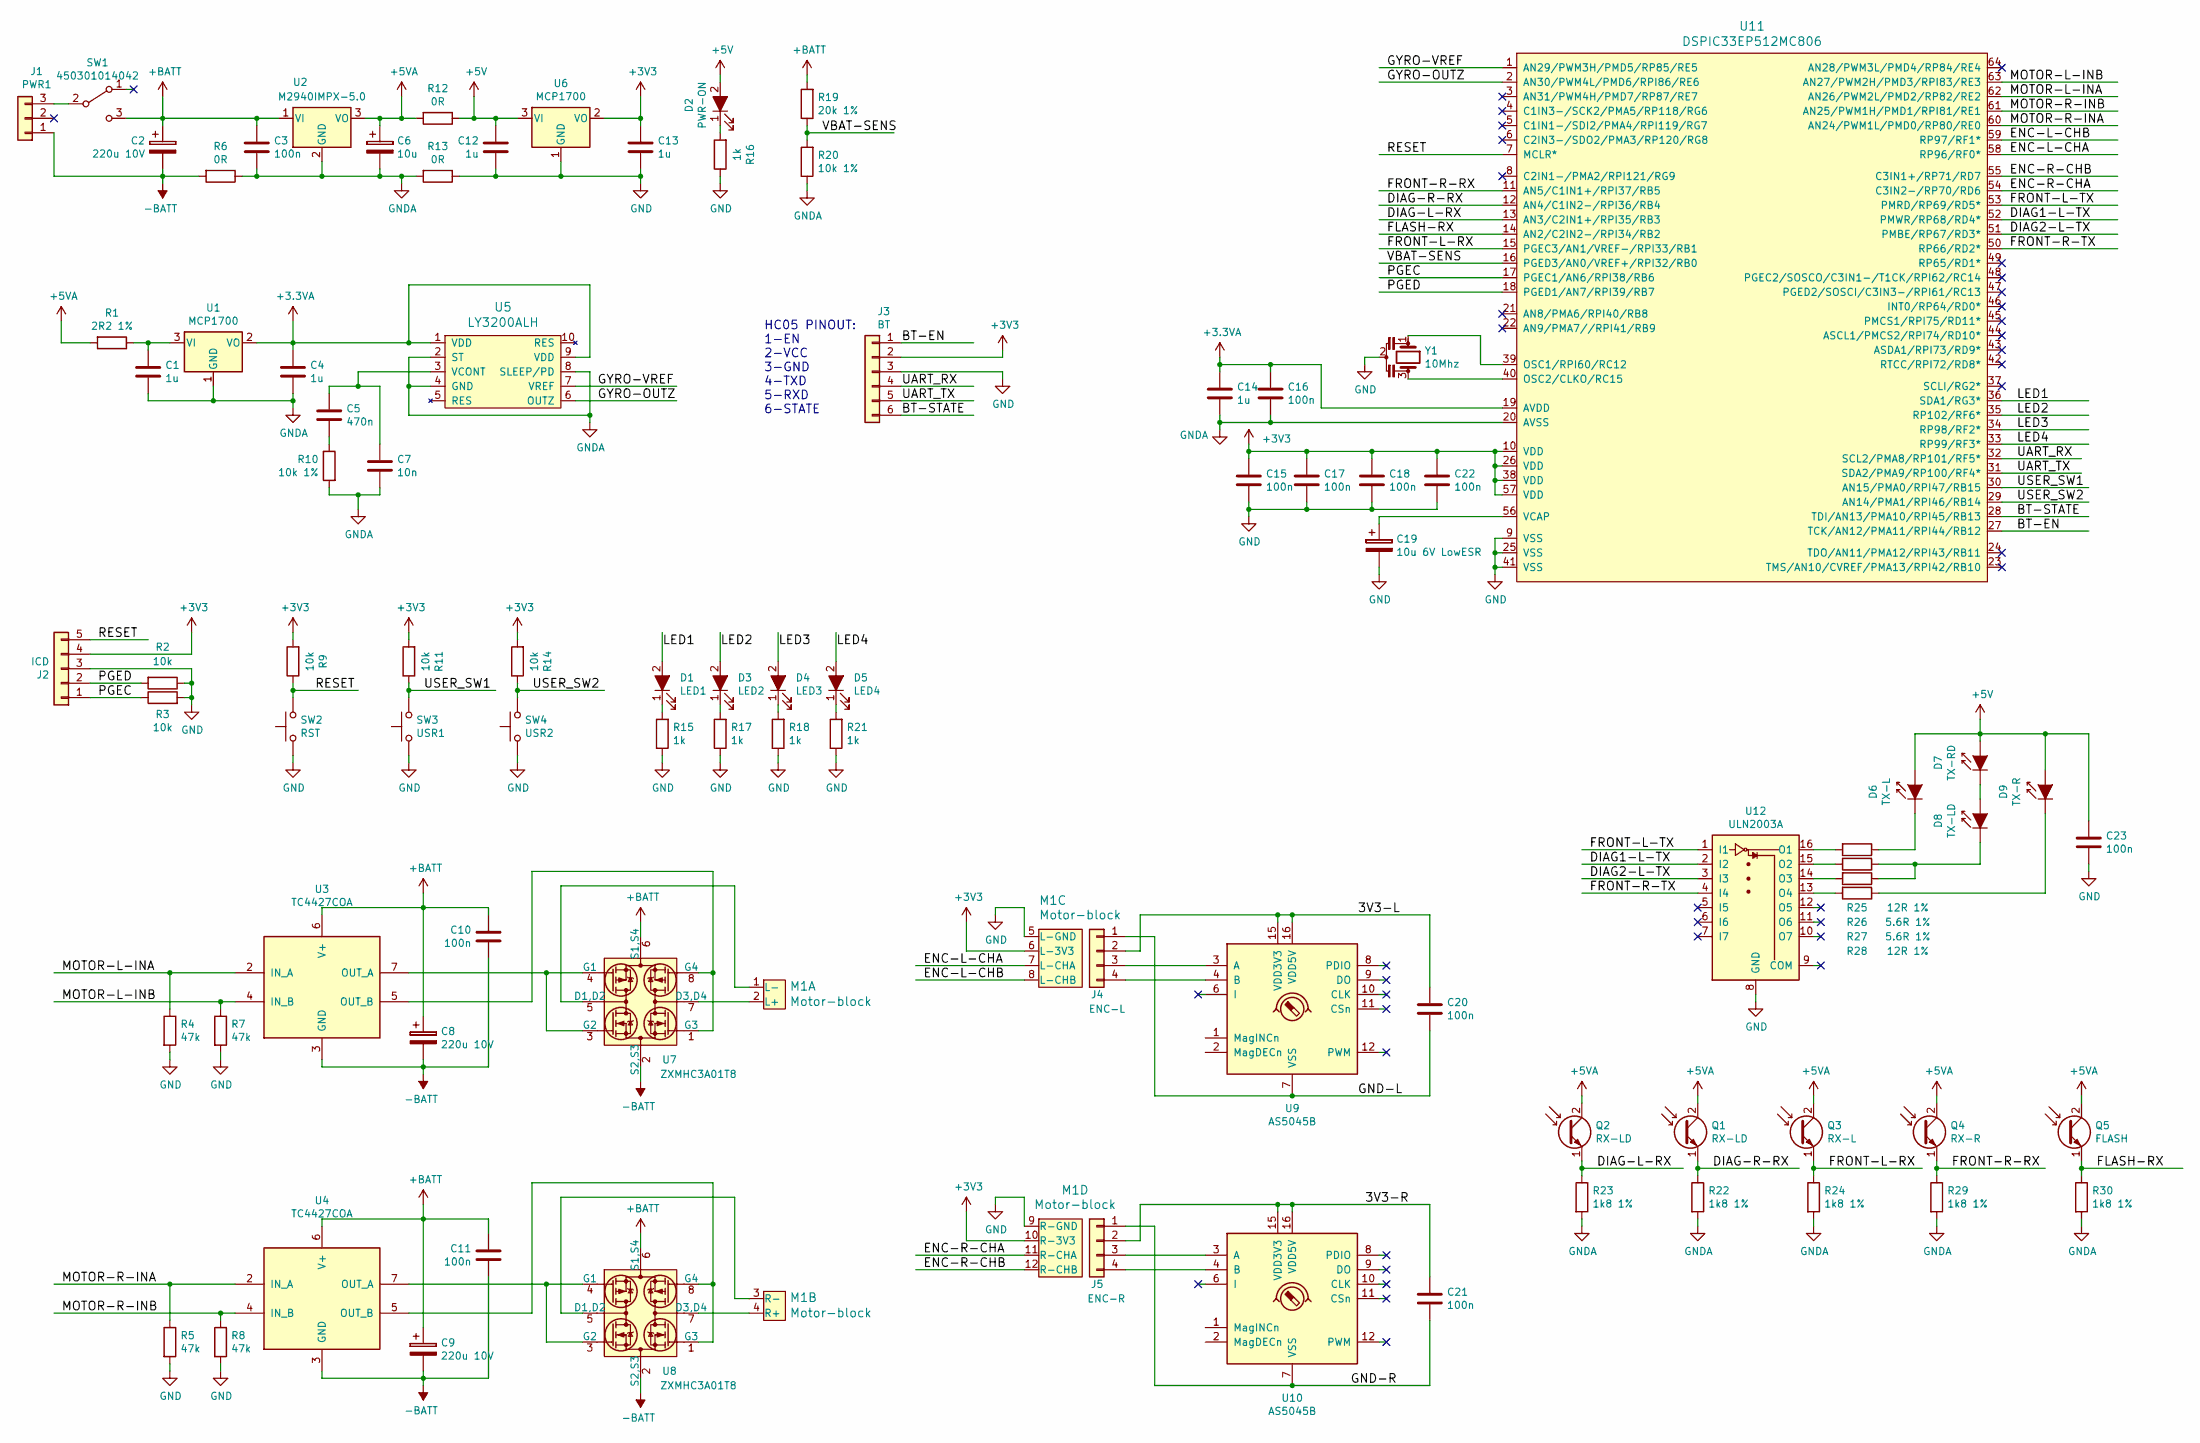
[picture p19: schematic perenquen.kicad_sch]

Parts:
C1, C4, C12, C13, C14: 1u; C_0805; MPN 08053G105ZAT2A
C2, C8, C9: 220u 10V; CP_Tantalum_Case-X_EIA-7343-43_Reflow; MPN T491D227K010AT
C3, C10, C11, C15, C16, C17, C18, C20, C21, C22, C23: 100n; C_0603; MPN 0603YC104KAT2A
C5: 470n; C_0603; MPN 0603YD474KAT2A
C6: 10u; C_0603; MPN T491C106M016AT
C7: 10n; C_0603; MPN 06035C103KAT2A
C19: 10u 6V LowESR; CP_Tantalum_Case-U_EIA-6032-15_Reflow; MPN T491C106M016AT
D1: LED1; D_0603; MPN SML-D12P8WT86
D2: PWR-ON; D_0603; MPN SML-D12V1WT86
D3: LED2; D_0603; MPN SML-D12P8WT86
D4: LED3; D_0603; MPN SML-D12P8WT86
D5: LED4; D_0603; MPN SML-D12P8WT86
D6: TX-L; LED_D5.0mm_Horizontal_O1.27mm_Z3.0mm; MPN SFH4545
D7: TX-RD; LED_D5.0mm_Horizontal_O1.27mm_Z3.0mm; MPN SFH4545
D8: TX-LD; LED_D5.0mm_Horizontal_O1.27mm_Z3.0mm; MPN SFH4545
D9: TX-R; LED_D5.0mm_Horizontal_O1.27mm_Z3.0mm; MPN SFH4545
J1: PWR1; JST_PH_B3B-PH-K_03x2.00mm_Straight; MPN B3B-PH-K-S(LF)(SN)
J2: ICD; Pin_Header_Angled_1x05_Pitch2.54mm; MPN 68016-410HLF
J3: BT; Socket_Strip_Straight_1x06_Pitch2.54mm; MPN 801-87-006-20-001101
J4: ENC-L; Pin_Header_Angled_1x04_Pitch2.54mm; MPN 68016-410HLF
J5: ENC-R; Pin_Header_Angled_1x04_Pitch2.54mm; MPN 68016-410HLF
M1: Motor-block; Perenquen-motor-block
Q1, Q2: RX-LD; LED_D3.0mm_Horizontal_O1.27mm_Z2.0mm; MPN TEFT4300
Q3: RX-L; LED_D3.0mm_Horizontal_O1.27mm_Z2.0mm; MPN TEFT4300
Q4: RX-R; LED_D3.0mm_Horizontal_O1.27mm_Z2.0mm; MPN TEFT4300
Q5: FLASH; LED_D3.0mm; MPN TEFT4300
R1: 2R2 1%; R_0603; MPN RC0603FR-072R2L
R2, R3, R9, R11, R14: 10k; R_0603; MPN RC0603FR-0710KL
R4, R5, R7, R8: 47k; R_0603; MPN RC0603JR-0747KL
R6, R12, R13: 0R; R_0805; MPN RC0805JR-070RL
R10, R20: 10k 1%; R_0603; MPN RC0603FR-0710KL
R15, R16, R17, R18, R21: 1k; R_0603; MPN RC0603JR-071KL
R19: 20k 1%; R_0603; MPN RC0603FR-0720KL
R22, R23, R24, R29, R30: 1k8 1%; R_0603; MPN RC0603FR-071K8L
R25, R28: 12R 1%; R_0805; MPN RC0805FR-0712RL
R26, R27: 5.6R 1%; R_0805; MPN RMCF0805FT5R60
SW1: 450301014042; Pin_Header_Straight_1x03_Pitch2.54mm; MPN 450301014042
SW2: RST; SW_SPST_B3U-1000P; MPN B3U-1000P
SW3: USR1; SW_SPST_B3U-1000P; MPN B3U-1000P
SW4: USR2; SW_SPST_B3U-1000P; MPN B3U-1000P
U1, U6: MCP1700; SOT-23; MPN MCP1700T-3302E/TT
U2: M2940IMPX-5.0; SOT-223-3_TabPin2; MPN LM2940IMPX-5.0/NOPB
U3, U4: TC4427COA; SOIC-8-N; MPN TC4427COA
U5: LY3200ALH; Gyro_ST_LGA10; MPN LY3200ALHTR
U7, U8: ZXMHC3A01T8; Zetex_SM8; MPN ZXMHC3A01T8TA
U9, U10: AS5045B; SSOP-16_5.3x6.2mm_Pitch0.65mm; MPN AS5045B
U11: DSPIC33EP512MC806; TQFP-64_10x10mm_Pitch0.5mm; MPN DSPIC33EP512MC806-I/PT
U12: ULN2003A; SSOP-16_4.4x5.2mm_Pitch0.65mm; MPN ULN2003APW
Y1: 10Mhz; Resonator_Murata_CSTCE_3pin; MPN CSTCE10M0G55-R0

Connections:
+3.3VA: C4.1, C14.1, C16.1, U1.2 (VO), U5.1 (VDD), U5.9 (VDD), U11.19 (AVDD)
+3V3: C13.1, C15.1, C17.1, C18.1, C22.1, J2.4, J3.2, M1.6 (L-3V3), M1.10 (R-3V3), R9.2, R11.2, R14.2, U6.2 (VO), U11.10 (VDD), U11.26 (VDD), U11.38 (VDD), U11.57 (VDD)
+5V: C12.1, C23.1, D2.2 (A), D6.2 (A), D7.2 (A), D9.2 (A), R12.1, U6.3 (VI)
+5VA: C6.1, Q1.2 (C), Q2.2 (C), Q3.2 (C), Q4.2 (C), Q5.2 (C), R1.2, R12.2, U2.3 (VO)
+BATT: C2.1, C3.1, C8.1, C9.1, C10.1, C11.1, R19.2, SW1.3 (C), U2.1 (VI), U3.6 (V+), U4.6 (V+), U7.6 (S1,S4), U8.6 (S1,S4)
-BATT: C2.2, C8.2, C9.2, C10.2, C11.2, J1.1, R6.2, U3.3 (GND), U4.3 (GND), U7.2 (S2,S3), U8.2 (S2,S3)
/3V3-L: C20.1, J4.2, U9.15 (VDD3V3), U9.16 (VDD5V)
/3V3-R: C21.1, J5.2, U10.15 (VDD3V3), U10.16 (VDD5V)
/BT-EN: J3.1, U11.27 (TCK/AN12/PMA11/RPI44/RB12)
/BT-STATE: J3.6, U11.28 (TDI/AN13/PMA10/RPI45/RB13)
/DIAG1-L-TX: U11.52 (PMWR/RP68/RD4*), U12.2 (I2)
/DIAG2-L-TX: U11.51 (PMBE/RP67/RD3*), U12.3 (I3)
/DIAG-L-RX: Q2.1 (E), R23.1, U11.13 (AN3/C2IN1+/RPI35/RB3)
/DIAG-R-RX: Q1.1 (E), R22.1, U11.12 (AN4/C1IN2-/RPI36/RB4)
/ENC-L-CHA: M1.7 (L-CHA), U11.58 (RP96/RF0*)
/ENC-L-CHB: M1.8 (L-CHB), U11.59 (RP97/RF1*)
/ENC-R-CHA: M1.11 (R-CHA), U11.54 (C3IN2-/RP70/RD6)
/ENC-R-CHB: M1.12 (R-CHB), U11.55 (C3IN1+/RP71/RD7)
/FLASH-RX: Q5.1 (E), R30.1, U11.14 (AN2/C2IN2-/RPI34/RB2)
/FRONT-L-RX: Q3.1 (E), R24.1, U11.15 (PGEC3/AN1/VREF-/RPI33/RB1)
/FRONT-L-TX: U11.53 (PMRD/RP69/RD5*), U12.1 (I1)
/FRONT-R-RX: Q4.1 (E), R29.1, U11.11 (AN5/C1IN1+/RPI37/RB5)
/FRONT-R-TX: U11.50 (RP66/RD2*), U12.4 (I4)
/GND-L: C20.2, J4.1, U9.7 (VSS)
/GND-R: C21.2, J5.1, U10.7 (VSS)
/GYRO-OUTZ: U5.6 (OUTZ), U11.2 (AN30/PWM4L/PMD6/RPI86/RE6)
/GYRO-VREF: U5.7 (VREF), U11.1 (AN29/PWM3H/PMD5/RP85/RE5)
/LED1: D1.2 (A), U11.36 (SDA1/RG3*)
/LED2: D3.2 (A), U11.35 (RP102/RF6*)
/LED3: D4.2 (A), U11.34 (RP98/RF2*)
/LED4: D5.2 (A), U11.33 (RP99/RF3*)
/MOTOR-L-INA: R4.1, U3.2 (IN_A), U11.62 (AN26/PWM2L/PMD2/RP82/RE2)
/MOTOR-L-INB: R7.1, U3.4 (IN_B), U11.63 (AN27/PWM2H/PMD3/RPI83/RE3)
/MOTOR-R-INA: R5.1, U4.2 (IN_A), U11.60 (AN24/PWM1L/PMD0/RP80/RE0)
/MOTOR-R-INB: R8.1, U4.4 (IN_B), U11.61 (AN25/PWM1H/PMD1/RPI81/RE1)
/PGEC: J2.1, R3.1, U11.17 (PGEC1/AN6/RPI38/RB6)
/PGED: J2.2, R2.2, U11.18 (PGED1/AN7/RPI39/RB7)
/RESET: J2.5, R9.1, SW2.2, U11.7 (MCLR*)
/UART_RX: J3.4, U11.32 (SCL2/PMA8/RP101/RF5*)
/UART_TX: J3.5, U11.31 (SDA2/PMA9/RP100/RF4*)
/USER_SW1: R11.1, SW3.2, U11.30 (AN15/PMA0/RPI47/RB15)
/USER_SW2: R14.1, SW4.2, U11.29 (AN14/PMA1/RPI46/RB14)
/VBAT-SENS: R19.1, R20.2, U11.16 (PGED3/AN0/VREF+/RPI32/RB0)
GND: C12.2, C13.2, C15.2, C17.2, C18.2, C19.2, C22.2, C23.2, J2.3, J3.3, M1.5 (L-GND), M1.9 (R-GND), R2.1, R3.2, R4.2, R5.2, R7.2, R8.2, R13.1, R15.1, R16.1, R17.1, R18.1, R21.1, SW2.1, SW3.1, SW4.1, U6.1 (GND), U11.9 (VSS), U11.25 (VSS), U11.41 (VSS), U12.8 (GND), Y1.2
GNDA: C1.2, C3.2, C4.2, C6.2, C7.2, C14.2, C16.2, R6.1, R10.2, R13.2, R20.1, R22.2, R23.2, R24.2, R29.2, R30.2, U1.1 (GND), U2.2 (GND), U5.2 (ST), U5.4 (GND), U5.8 (SLEEP/PD), U11.20 (AVSS)
unnamed: C1.1, R1.1, U1.3 (VI)
unnamed: C5.1, C7.1, U5.3 (VCONT)
unnamed: C5.2, R10.1
unnamed: C19.1, U11.56 (VCAP)
unnamed: D1.1 (K), R15.2
unnamed: D2.1 (K), R16.2
unnamed: D3.1 (K), R17.2
unnamed: D4.1 (K), R18.2
unnamed: D5.1 (K), R21.2
unnamed: D6.1 (K), R25.1
unnamed: D7.1 (K), D8.2 (A)
unnamed: D8.1 (K), R26.1, R27.1
unnamed: D9.1 (K), R28.1
unnamed: J1.3, SW1.2 (B)
unnamed: J4.3, U9.3 (A)
unnamed: J4.4, U9.4 (B)
unnamed: J5.3, U10.3 (A)
unnamed: J5.4, U10.4 (B)
unnamed: M1.1 (L-), U7.5 (D1,D2)
unnamed: M1.2 (L+), U7.7 (D3,D4)
unnamed: M1.3 (R-), U8.5 (D1,D2)
unnamed: M1.4 (R+), U8.7 (D3,D4)
unnamed: R25.2, U12.16 (O1)
unnamed: R26.2, U12.15 (O2)
unnamed: R27.2, U12.14 (O3)
unnamed: R28.2, U12.13 (O4)
unnamed: U3.5 (OUT_B), U7.1 (G3), U7.8 (G4)
unnamed: U3.7 (OUT_A), U7.3 (G2), U7.4 (G1)
unnamed: U4.5 (OUT_B), U8.1 (G3), U8.8 (G4)
unnamed: U4.7 (OUT_A), U8.3 (G2), U8.4 (G1)
unnamed: U11.39 (OSC1/RPI60/RC12), Y1.1
unnamed: U11.40 (OSC2/CLKO/RC15), Y1.3

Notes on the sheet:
HC05 PINOUT: 1-EN 2-VCC 3-GND 4-TXD 5-RXD 6-STATE

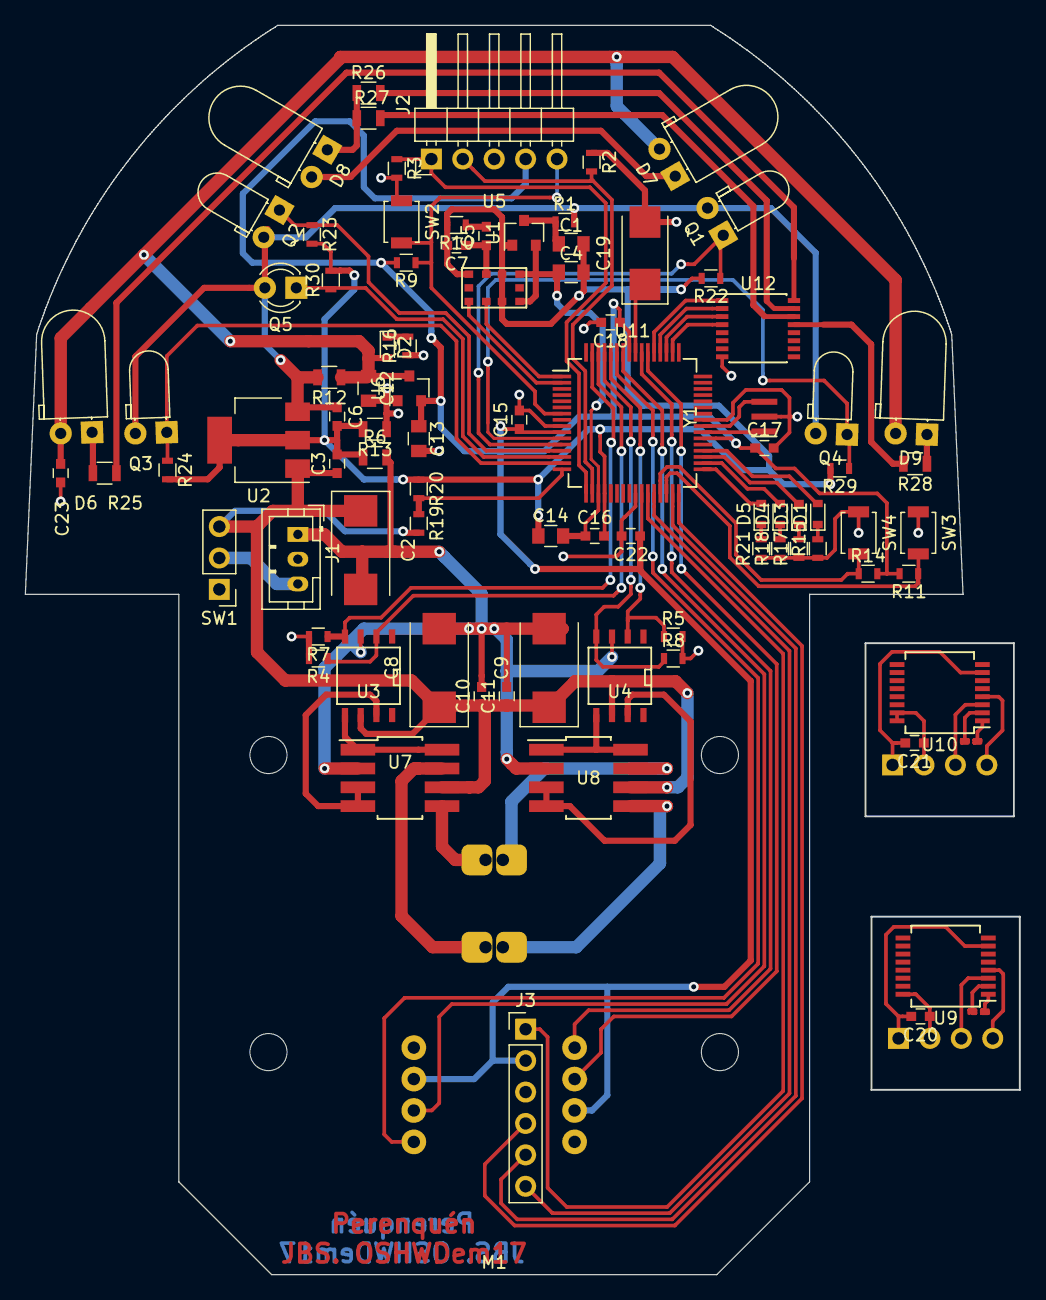
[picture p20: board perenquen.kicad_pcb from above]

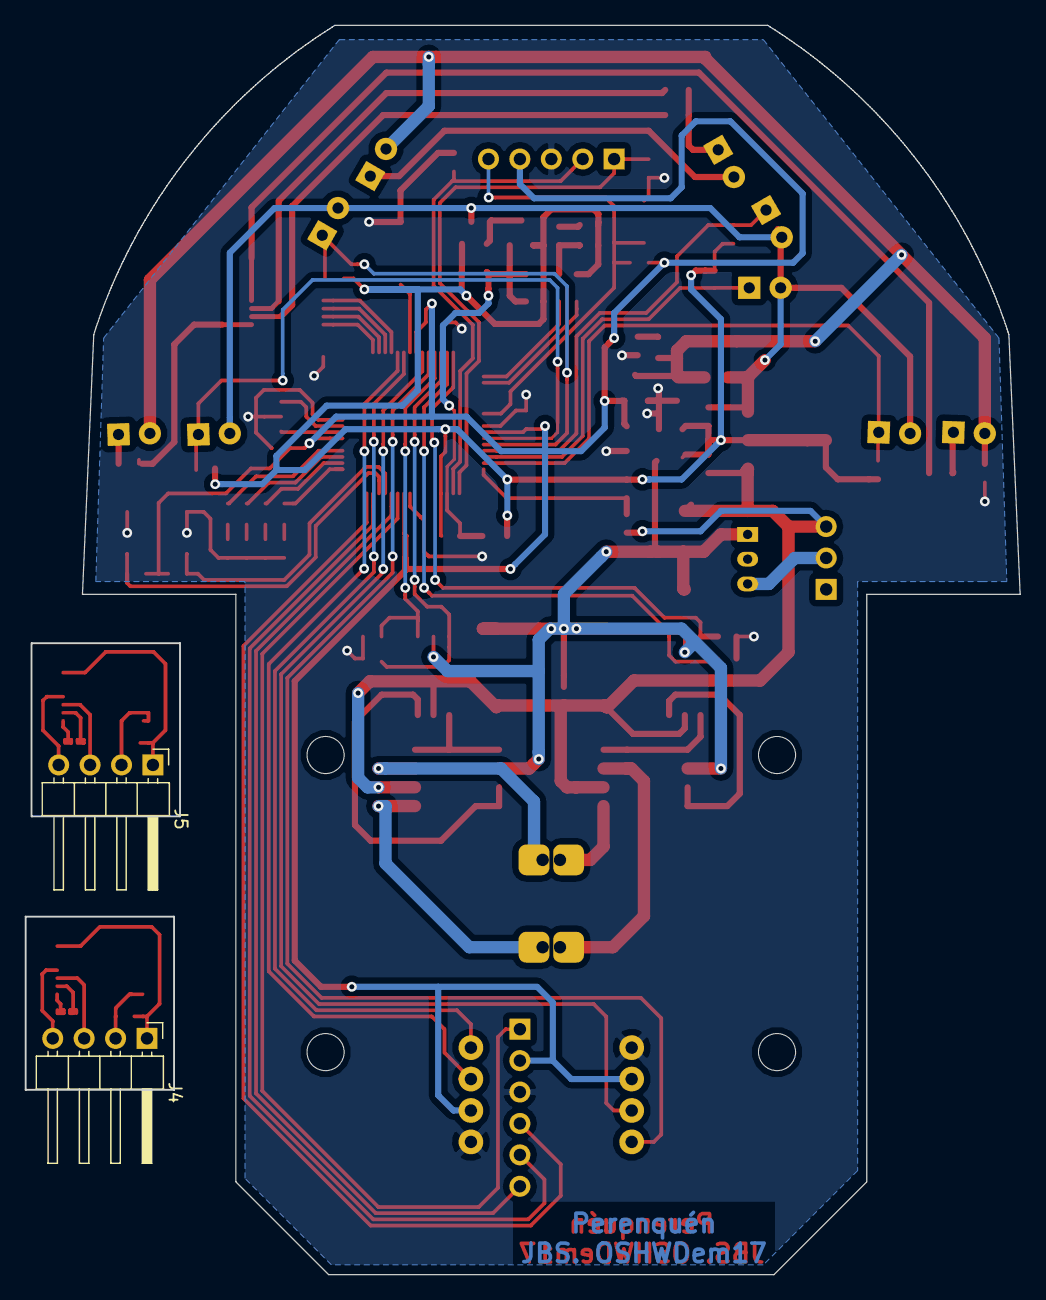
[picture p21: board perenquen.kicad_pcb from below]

Board: 2 copper layers, 80.4 x 101.0 mm, 90 parts (2 on the bottom side), 77 nets.

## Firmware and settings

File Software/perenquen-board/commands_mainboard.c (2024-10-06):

/*
 *  Copyright Droids Corporation (2009)
 *
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
 *  Revision : $Id$
 *
 *  Olivier MATZ <zer0@droids-corp.org>
 */

/*
 *  Copyright Javier Baliñas Santos (2018)
 *  Javier Balias Santos <javier@arc-robots.org>
 *
 *  Code ported to family of microcontrollers dsPIC from
 *  commands_mainboard.c,v 1.8 2009/05/27 20:04:07 zer0 Exp.
 */

#include <stdio.h>
#include <string.h>

#include <aversive/pgmspace.h>
#include <aversive/wait.h>
#include <aversive/error.h>

#include <uart.h>


#include <clock_time.h>


#include <pid.h>
#include <quadramp.h>
#include <control_system_manager.h>
#include <trajectory_manager.h>
#include <vect_base.h>
#include <lines.h>
#include <polygon.h>

#include <blocking_detection_manager.h>
#include <robot_system.h>
#include <position_manager.h>

#ifdef HOST_VERSION
#include <hostsim.h>
#endif

#include <rdline.h>
#include <parse.h>
#include <parse_string.h>
#include <parse_num.h>



#include "main.h"
#include "sensor.h"
#include "cmdline.h"
#include "strat.h"
#include "strat_utils.h"
#include "strat_base.h"

#include "actuator.h"
//

#include "robotsim.h"
#include "strat_base.h"

#include "strat_utils.h"

#ifdef HOST_VERSION
#define COMPILE_COMMANDS_MAINBOARD_OPTIONALS
#endif

uint8_t strat_obstacle(void)
{
  #define S_FRONT_OBSTACLE_VALUE 350
  sensor_adc_do_read(S_ADC_FRONT_LEFT);
  sensor_adc_do_read(S_ADC_FRONT_RIGHT);
  return (sensor_adc_get_value_on(S_ADC_FRONT_LEFT) > S_FRONT_OBSTACLE_VALUE &&
          sensor_adc_get_value_on(S_ADC_FRONT_RIGHT) > S_FRONT_OBSTACLE_VALUE);
}

void strat_follow_wall(uint8_t side, int32_t gain)
{
  #define STATE_CALIB         0
  #define STATE_WAITING_START 1
  #define STATE_GO_FORWARD    2
  #define STATE_WALL_TRACKER  3
  #define STATE_TURN          4
  #define STATE_TURN_END      5

  #define S_FRONT_START_VALUE     200
  #define S_FRONT_END_TURN_VALUE  150

  uint8_t state = STATE_CALIB;
  int16_t calib_diag_left=0, calib_diag_right=0;
  int16_t error;
  float angle = 0.0;
  uint8_t err;
  uint8_t running = 1;
  uint8_t sensor;


  double coef;
  #define RADIOUS_mm  80.0
	coef = 2. * RADIOUS_mm / EXT_TRACK_MM;
  trajectory_set_speed(&mainboard.traj, mainboard.traj.d_speed, mainboard.traj.d_speed/coef);

  DEBUG(E_USER_STRAT, "coef %f, speed d = %d, a = %d\n\r", coef, mainboard.traj.d_speed, mainboard.traj.a_speed);


  interrupt_traj_reset();

  while (running)
  {
    switch(state) {
      case STATE_CALIB:
        sensor_adc_do_read(S_ADC_DIAG_LEFT);
        sensor_adc_do_read(S_ADC_DIAG_RIGHT);
        calib_diag_left = sensor_adc_get_value_on(S_ADC_DIAG_LEFT);
        calib_diag_right = sensor_adc_get_value_on(S_ADC_DIAG_RIGHT);
        DEBUG(E_USER_STRAT, "calib left %d\n\r", calib_diag_left);
        DEBUG(E_USER_STRAT, "calib right %d\n\r", calib_diag_right);
        state = STATE_WAITING_START;
        break;

      case STATE_WAITING_START:
        sensor_adc_do_read(S_ADC_FRONT_LEFT);
        sensor_adc_do_read(S_ADC_FRONT_RIGHT);
        DEBUG(E_USER_STRAT, "Waiting START...\n\r");
        while(sensor_adc_get_value_on(S_ADC_FRONT_LEFT) < S_FRONT_START_VALUE &&
              sensor_adc_get_value_on(S_ADC_FRONT_RIGHT) < S_FRONT_START_VALUE)
        {
          sensor_adc_do_read(S_ADC_FRONT_LEFT);
          sensor_adc_do_read(S_ADC_FRONT_RIGHT);
          time_wait_ms(100);
        }
        while(sensor_adc_get_value_on(S_ADC_FRONT_LEFT) > S_FRONT_START_VALUE ||
              sensor_adc_get_value_on(S_ADC_FRONT_RIGHT) > S_FRONT_START_VALUE)
        {
          sensor_adc_do_read(S_ADC_FRONT_LEFT);
          sensor_adc_do_read(S_ADC_FRONT_RIGHT);
          time_wait_ms(100);
        }

        DEBUG(E_USER_STRAT, "GO!!!!\n\r");
        state = STATE_GO_FORWARD;
        break;

      case STATE_GO_FORWARD:
        trajectory_d_rel(&mainboard.traj, 30000);
        DEBUG(E_USER_STRAT, "Go forward\n\r");
        state = STATE_WALL_TRACKER;
        break;

      case STATE_WALL_TRACKER:

        /* Wall tracker */
        //time_wait_ms(100);
        if (side == SIDE_LEFT) {
          sensor_adc_do_read(S_ADC_DIAG_LEFT);

          error = calib_diag_left - sensor_adc_get_value_on(S_ADC_DIAG_LEFT);

          if (error >  (calib_diag_left/3))
            angle = 180;
          else
            angle = error*gain/1024;
          DEBUG(E_USER_STRAT, "LEFT error %d, angle %f\n\r", error, angle);

          trajectory_only_a_rel(&mainboard.traj, (int32_t)angle);
        }
        else {
          sensor_adc_do_read(S_ADC_DIAG_RIGHT);

          error = calib_diag_right - sensor_adc_get_value_on(S_ADC_DIAG_RIGHT);

          if (error >  (calib_diag_right/3))
            angle = -180;
          else
            angle = -error*gain/1024;

          DEBUG(E_USER_STRAT, "RIGHT error %d, angle %f\n\r", error, angle);

          trajectory_only_a_rel(&mainboard.traj, (int32_t)angle);
        }

        /* End traj */
        err = test_traj_end(END_TRAJ|END_OBSTACLE|END_INTR);
        if(err == END_TRAJ) {
          DEBUG(E_USER_STRAT, "traj returns END_TRAJ\n\r");
          state = STATE_GO_FORWARD;
        }
        else if(err == END_OBSTACLE) {
          DEBUG(E_USER_STRAT, "traj returns END_OBSTACLE\n\r");
          state = STATE_TURN;
          //running = 0;
        }
        else if(err == END_INTR) {
          DEBUG(E_USER_STRAT, "traj returns END_INTR\n\r");
          //running = 0;
        }
        break;

      case STATE_TURN:
        trajectory_a_rel(&mainboard.traj, (side==SIDE_LEFT? -270:270));
        DEBUG(E_USER_STRAT, "Turn %d start\n\r", (side==SIDE_LEFT? -270:270));
        state = STATE_TURN_END;
        break;

      case STATE_TURN_END:
        DEBUG(E_USER_STRAT, "Waiting turn end...\n\r");
        sensor = (side==SIDE_LEFT? S_ADC_FRONT_LEFT : S_ADC_FRONT_RIGHT);
        sensor_adc_do_read(sensor);
        err = 0;
        while(sensor_adc_get_value_on(sensor) > S_FRONT_END_TURN_VALUE && err == 0) {
          sensor_adc_do_read(sensor);
          err = test_traj_end(END_TRAJ);
        }

        if(err == END_TRAJ) {
          DEBUG(E_USER_STRAT, "traj returns END_TRAJ\n\r");
          state = STATE_TURN;
          break;
        }

        trajectory_hardstop(&mainboard.traj);
        //time_wait_ms(100);
        DEBUG(E_USER_STRAT, "Turn end\n\r");
        state = STATE_GO_FORWARD;
        break;

      default:
        break;
    }
  }
}

struct cmd_event_result
{
    fixed_string_t arg0;
    fixed_string_t arg1;
    fixed_string_t arg2;
};

/* function called when cmd_event is parsed successfully */
static void cmd_event_parsed(void *parsed_result, void *data)
{
    uint16_t bit = 0;

    struct cmd_event_result * res = parsed_result;

    if (!strcmp_P(res->arg1, PSTR("all")))
    {
        bit = DO_ENCODERS | DO_CS | DO_RS | DO_POS | DO_BD | DO_TIMER | DO_POWER | DO_TM_DATA;
        if (!strcmp_P(res->arg2, PSTR("on")))
            mainboard.flags |= bit;
        else if (!strcmp_P(res->arg2, PSTR("off")))
            mainboard.flags &= bit;
        else
        { /* show */
            printf_P(PSTR("encoders is %s\r\n"),
                     (DO_ENCODERS & mainboard.flags) ? "on" : "off");
            printf_P(PSTR("cs is %s\r\n"),
                     (DO_CS & mainboard.flags) ? "on" : "off");
            printf_P(PSTR("rs is %s\r\n"),
                     (DO_RS & mainboard.flags) ? "on" : "off");
            printf_P(PSTR("pos is %s\r\n"),
                     (DO_POS & mainboard.flags) ? "on" : "off");
            printf_P(PSTR("bd is %s\r\n"),
                     (DO_BD & mainboard.flags) ? "on" : "off");
            printf_P(PSTR("timer is %s\r\n"),
                     (DO_TIMER & mainboard.flags) ? "on" : "off");
            printf_P(PSTR("power is %s\r\n"),
                     (DO_POWER & mainboard.flags) ? "on" : "off");
            printf_P(PSTR("tm is %s\r\n"),
                     (DO_TM_DATA & mainboard.flags) ? "on" : "off");
        }
        return;
    }

    if (!strcmp_P(res->arg1, PSTR("encoders")))
        bit = DO_ENCODERS;
    else if (!strcmp_P(res->arg1, PSTR("cs")))
    {
        strat_hardstop();
        bit = DO_CS;
    }
    else if (!strcmp_P(res->arg1, PSTR("rs")))
        bit = DO_RS;
    else if (!strcmp_P(res->arg1, PSTR("pos")))
        bit = DO_POS;
    else if (!strcmp_P(res->arg1, PSTR("bd")))
        bit = DO_BD;
    else if (!strcmp_P(res->arg1, PSTR("timer")))
    {
        time_reset();
        bit = DO_TIMER;
    }
    else if (!strcmp_P(res->arg1, PSTR("power")))
        bit = DO_POWER;
    else if (!strcmp_P(res->arg1, PSTR("tm")))
        bit = DO_TM_DATA;

    if (!strcmp_P(res->arg2, PSTR("on")))
        mainboard.flags |= bit;
    else if (!strcmp_P(res->arg2, PSTR("off")))
    {
        if (!strcmp_P(res->arg1, PSTR("cs")))
        {
#ifdef HOST_VERSION
            robotsim_pwm(MOTOR_LEFT, 0);
            robotsim_pwm(MOTOR_RIGHT, 0);
#else
            hspwm_set_pwm(MOTOR_LEFT, 0);
          	hspwm_set_pwm(MOTOR_RIGHT, 0);
#endif
        }
        mainboard.flags &= (~bit);
    }
    printf_P(PSTR("%s is %s\r\n"), res->arg1,
             (bit & mainboard.flags) ? "on" : "off");
}

prog_char str_event_arg0[] = "event";
parse_pgm_token_string_t cmd_event_arg0 = TOKEN_STRING_INITIALIZER(struct cmd_event_result, arg0, str_event_arg0);
prog_char str_event_arg1[] = "all#encoders#cs#rs#pos#bd#timer#power#tm";
parse_pgm_token_string_t cmd_event_arg1 = TOKEN_STRING_INITIALIZER(struct cmd_event_result, arg1, str_event_arg1);
prog_char str_event_arg2[] = "on#off#show";
parse_pgm_token_string_t cmd_event_arg2 = TOKEN_STRING_INITIALIZER(struct cmd_event_result, arg2, str_event_arg2);

prog_char help_event[] = "Enable/disable events";
parse_pgm_inst_t cmd_event = {
    .f = cmd_event_parsed, /* function to call */
    .data = NULL, /* 2nd arg of func */
    //.help_str = help_event,
    .tokens =
    { /* token list, NULL terminated */
        (prog_void *) & cmd_event_arg0,
        (prog_void *) & cmd_event_arg1,
        (prog_void *) & cmd_event_arg2,
        NULL,
    },
};

/**********************************************************/
/* Init match */

/* from commands_traj.c */
//void auto_position(void);

/* this structure is filled when cmd_init is parsed successfully */
struct cmd_init_result
{
    fixed_string_t arg0;
    fixed_string_t color;
};


/* function called when cmd_init is parsed successfully */
static void cmd_init_parsed(void *parsed_result, void *data)
{
    //struct cmd_init_result *res = parsed_result;

	/* autopos main robot */
	//auto_position();

	time_wait_ms (200);

	printf ("Done\n\r");
}

prog_char str_init_arg0[] = "init";
parse_pgm_token_string_t cmd_init_arg0 = TOKEN_STRING_INITIALIZER(struct cmd_init_result, arg0, str_init_arg0);
prog_char str_init_color[] = "left#righ";
parse_pgm_token_string_t cmd_init_color = TOKEN_STRING_INITIALIZER(struct cmd_init_result, color, str_init_color);

prog_char help_init[] = "Init the robots";
parse_pgm_inst_t cmd_init = {
    .f = cmd_init_parsed, /* function to call */
    .data = NULL, /* 2nd arg of func */
    //.help_str = help_init,
    .tokens =
    { /* token list, NULL terminated */
        (prog_void *) & cmd_init_arg0,
        (prog_void *) & cmd_init_color,
        NULL,
    },
};



/**********************************************************/
/* Start */

/* this structure is filled when cmd_start is parsed successfully */
struct cmd_start_result
{
    fixed_string_t arg0;
    fixed_string_t strategy;
    int32_t arg2;
    //fixed_string_t debug;
};

/* function called when cmd_start is parsed successfully */
static void cmd_start_parsed(void *parsed_result, void *data)
{
    struct cmd_start_result *res = parsed_result;

    if (!strcmp_P(res->strategy, PSTR("left")))
      strat_follow_wall(SIDE_LEFT, res->arg2);
    else
      strat_follow_wall(SIDE_RIGHT, res->arg2);

    // OK speed 1000 gain 100
    // OK speed 1500 gain 200

    //uint8_t old_level = gen.log_level;
    //int8_t c;

    // TODO
    //gen.logs[NB_LOGS] = E_USER_STRAT;
    //if (!strcmp_P(res->debug, PSTR("debug")))
    //{
    //    strat_infos.dump_enabled = 1;
    //    gen.log_level = 5;
    //}
    //else if (!strcmp_P(res->debug, PSTR("step_debug")))
    //{
    //    strat_infos.dump_enabled = 1;
    //    strat_infos.debug_step = 1;
    //    gen.log_level = 5;
    //}
    //else
    //{
    //    strat_infos.dump_enabled = 0;
    //    gen.log_level = 0;
    //}

    //strat_dump_conf();

    //strat_start();

    //gen.logs[NB_LOGS] = 0;
    //gen.log_level = old_level;
}

prog_char str_start_arg0[] = "start";
parse_pgm_token_string_t cmd_start_arg0 = TOKEN_STRING_INITIALIZER(struct cmd_start_result, arg0, str_start_arg0);
prog_char str_start_strategy[] = "left#right";
parse_pgm_token_string_t cmd_start_strategy = TOKEN_STRING_INITIALIZER(struct cmd_start_result, strategy, str_start_strategy);
parse_pgm_token_num_t cmd_start_arg2 = TOKEN_NUM_INITIALIZER(struct cmd_start_result, arg2, INT32);

//prog_char str_start_debug[] = "debug#step_debug#match";
//parse_pgm_token_string_t cmd_start_debug = TOKEN_STRING_INITIALIZER(struct cmd_start_result, debug, str_start_debug);

prog_char help_start[] = "Start the robot";
parse_pgm_inst_t cmd_start = {
    .f = cmd_start_parsed, /* function to call */
    .data = NULL, /* 2nd arg of func */
    //.help_str = help_start,
    .tokens =
    { /* token list, NULL terminated */
        (prog_void *) & cmd_start_arg0,
        (prog_void *) & cmd_start_strategy,
        (prog_void *) & cmd_start_arg2,
        //(prog_void *) & cmd_start_debug,
        NULL,
    },
};



#ifdef COMPILE_COMMANDS_MAINBOARD_OPTIONALS /*--------------------------------*/

/**********************************************************/
/* Interact */

/* this structure is filled when cmd_interact is parsed successfully */
struct cmd_interact_result
{
    fixed_string_t arg0;
};

static void print_cs(void)
{
    printf_P(PSTR("cons_d=% .8"PRIi32" cons_a=% .8"PRIi32" fil_d=% .8"PRIi32" fil_a=% .8"PRIi32" "
                  "err_d=% .8"PRIi32" err_a=% .8"PRIi32" out_d=% .8"PRIi32" out_a=% .8"PRIi32"\r\n"),
             cs_get_consign(&mainboard.distance.cs),
             cs_get_consign(&mainboard.angle.cs),
             cs_get_filtered_consign(&mainboard.distance.cs),
             cs_get_filtered_consign(&mainboard.angle.cs),
             cs_get_error(&mainboard.distance.cs),
             cs_get_error(&mainboard.angle.cs),
             cs_get_out(&mainboard.distance.cs),
             cs_get_out(&mainboard.angle.cs));
}

static void print_pos(void)
{
    printf_P(PSTR("x=% .8d y=% .8d a=% .8d\r\n"),
             position_get_x_s16(&mainboard.pos),
             position_get_y_s16(&mainboard.pos),
             position_get_a_deg_s16(&mainboard.pos));
}

static void print_time(void)
{
    printf_P(PSTR("time %d\r\n"), (int16_t) time_get_s());
}

static void print_sensors(void)
{
#ifdef notyet
    if (sensor_start_switch())
        printf_P(PSTR("Start switch | "));
    else
        printf_P(PSTR("             | "));

    if (IR_DISP_SENSOR())
        printf_P(PSTR("IR disp | "));
    else
        printf_P(PSTR("        | "));

    printf_P(PSTR("\r\n"));
#endif
}

static void print_pid(void)
{
    printf_P(PSTR("P=% .8"PRIi32" I=% .8"PRIi32" D=% .8"PRIi32" out=% .8"PRIi32" | "
                  "P=% .8"PRIi32" I=% .8"PRIi32" D=% .8"PRIi32" out=% .8"PRIi32"\r\n"),
             pid_get_value_in(&mainboard.distance.pid) * pid_get_gain_P(&mainboard.distance.pid),
             pid_get_value_I(&mainboard.distance.pid) * pid_get_gain_I(&mainboard.distance.pid),
             pid_get_value_D(&mainboard.distance.pid) * pid_get_gain_D(&mainboard.distance.pid),
             pid_get_value_out(&mainboard.distance.pid),
             pid_get_value_in(&mainboard.angle.pid) * pid_get_gain_P(&mainboard.angle.pid),
             pid_get_value_I(&mainboard.angle.pid) * pid_get_gain_I(&mainboard.angle.pid),
             pid_get_value_D(&mainboard.angle.pid) * pid_get_gain_D(&mainboard.angle.pid),
             pid_get_value_out(&mainboard.angle.pid));
}

#define PRINT_POS       (1<<0)
#define PRINT_PID       (1<<1)
#define PRINT_CS        (1<<2)
#define PRINT_SENSORS   (1<<3)
#define PRINT_TIME      (1<<4)
#define PRINT_BLOCKING  (1<<5)

static void cmd_interact_parsed(void * parsed_result, void * data)
{
    int c;
    int8_t cmd;
    uint8_t print = 0;
    struct vt100 vt100;

    vt100_init(&vt100);

    printf_P(PSTR("Display debugs:\r\n"
                  "  1:pos\r\n"
                  "  2:pid\r\n"
                  "  3:cs\r\n"
                  "  4:sensors\r\n"
                  "  5:time\r\n"
                  /* "  6:blocking\r\n" */
                  "Commands:\r\n"
                  "  arrows:move\r\n"
                  "  space:stop\r\n"
                  "  q:quit\r\n"));

    /* stop motors */
    mainboard.flags &= (~DO_CS);
    motor_pwm_set_and_save(MOTOR_LEFT, 0);
    motor_pwm_set_and_save(MOTOR_RIGHT, 0);

    while (1)
    {
        if (print & PRINT_POS)
        {
            print_pos();
        }

        if (print & PRINT_PID)
        {
            print_pid();
        }

        if (print & PRINT_CS)
        {
            print_cs();
        }

        if (print & PRINT_SENSORS)
        {
            print_sensors();
        }

        if (print & PRINT_TIME)
        {
            print_time();
        }
        /* 		if (print & PRINT_BLOCKING) { */
        /* 			printf_P(PSTR("%s %s blocking=%d\r\n"),  */
        /* 				 mainboard.blocking ? "BLOCK1":"      ", */
        /* 				 rs_is_blocked(&mainboard.rs) ? "BLOCK2":"      ", */
        /* 				 rs_get_blocking(&mainboard.rs)); */
        /* 		} */

        c = cmdline_getchar();
        if (c == -1)
        {
            wait_ms(10);
            continue;
        }
        cmd = vt100_parser(&vt100, c);
        if (cmd == -2)
        {
            wait_ms(10);
            continue;
        }

        if (cmd == -1)
        {
            switch (c)
            {
            case '1': print ^= PRINT_POS;
                break;
            case '2': print ^= PRINT_PID;
                break;
            case '3': print ^= PRINT_CS;
                break;
            case '4': print ^= PRINT_SENSORS;
                break;
            case '5': print ^= PRINT_TIME;
                break;
            case '6': print ^= PRINT_BLOCKING;
                break;

            case 'q':
                if (mainboard.flags & DO_CS)
                    strat_hardstop();
                motor_pwm_set_and_save(MOTOR_LEFT, 0);
                motor_pwm_set_and_save(MOTOR_RIGHT, 0);
                return;
            case ' ':
                motor_pwm_set_and_save(MOTOR_LEFT, 0);
                motor_pwm_set_and_save(MOTOR_RIGHT, 0);
                break;
            default:
                break;
            }
        }
        else
        {
#ifdef HOST_VERSION
#define PWM_INTERACT 1200
#else
#define PWM_INTERACT 1200
#endif
            switch (cmd)
            {
            case KEY_UP_ARR:
                motor_pwm_set_and_save(MOTOR_LEFT, PWM_INTERACT);
                motor_pwm_set_and_save(MOTOR_RIGHT, PWM_INTERACT);
                break;
            case KEY_LEFT_ARR:
                motor_pwm_set_and_save(MOTOR_LEFT, -PWM_INTERACT);
                motor_pwm_set_and_save(MOTOR_RIGHT, PWM_INTERACT);
                break;
            case KEY_DOWN_ARR:
                motor_pwm_set_and_save(MOTOR_LEFT, -PWM_INTERACT);
                motor_pwm_set_and_save(MOTOR_RIGHT, -PWM_INTERACT);
                break;
            case KEY_RIGHT_ARR:
                motor_pwm_set_and_save(MOTOR_LEFT, PWM_INTERACT);
                motor_pwm_set_and_save(MOTOR_RIGHT, -PWM_INTERACT);
                break;
            }
        }
        wait_ms(10);
    }
}

prog_char str_interact_arg0[] = "interact";
parse_pgm_token_string_t cmd_interact_arg0 = TOKEN_STRING_INITIALIZER(struct cmd_interact_result, arg0, str_interact_arg0);

prog_char help_interact[] = "Interactive mode";
parse_pgm_inst_t cmd_interact = {
    .f = cmd_interact_parsed, /* function to call */
    .data = NULL, /* 2nd arg of func */
    //.help_str = help_interact,
    .tokens =
    { /* token list, NULL terminated */
        (prog_void *) & cmd_interact_arg0,
        NULL,
    },
};



/**********************************************************/
/* Rs tests */

/* this structure is filled when cmd_rs is parsed successfully */
struct cmd_rs_result
{
    fixed_string_t arg0;
    fixed_string_t arg1;
};

/* function called when cmd_rs is parsed successfully */
static void cmd_rs_parsed(void *parsed_result, void *data)
{
    //	struct cmd_rs_result *res = parsed_result;
    do
    {
        printf_P(PSTR("angle cons=% .6"PRIi32" in=% .6"PRIi32" out=% .6"PRIi32" / "),
                 cs_get_consign(&mainboard.angle.cs),
                 cs_get_filtered_feedback(&mainboard.angle.cs),
                 cs_get_out(&mainboard.angle.cs));
        printf_P(PSTR("distance cons=% .6"PRIi32" in=% .6"PRIi32" out=% .6"PRIi32" / "),
                 cs_get_consign(&mainboard.distance.cs),
                 cs_get_filtered_feedback(&mainboard.distance.cs),
                 cs_get_out(&mainboard.distance.cs));
        printf_P(PSTR("l=% .4"PRIi32" r=% .4"PRIi32"\r\n"), mainboard.motor_pwm_left,
                 mainboard.motor_pwm_right);
        wait_ms(100);
    }
    while (!cmdline_keypressed());
}

prog_char str_rs_arg0[] = "rs";
parse_pgm_token_string_t cmd_rs_arg0 = TOKEN_STRING_INITIALIZER(struct cmd_rs_result, arg0, str_rs_arg0);
prog_char str_rs_arg1[] = "show";
parse_pgm_token_string_t cmd_rs_arg1 = TOKEN_STRING_INITIALIZER(struct cmd_rs_result, arg1, str_rs_arg1);
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

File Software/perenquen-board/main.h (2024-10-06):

/*
 *  Copyright Javier Baliñas Santos (2024)
 *
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
 *  Revision : $Id$
 *
 *  Javier Baliñas Santos <balinas@gmail.com>
 */

#ifndef _MAIN_H_
#define _MAIN_H_


#include <aversive.h>
#include <aversive/error.h>

#include <clock_time.h>
#include <rdline.h>

#include <encoders_dspic.h>

#include <pid.h>
#include <quadramp.h>
#include <control_system_manager.h>
#include <blocking_detection_manager.h>
#include <robot_system.h>
#include <position_manager.h>
#include <trajectory_manager.h>

/** Robot dimensions */
#define ROBOT_LENGTH            101.1
#define ROBOT_WIDTH             75.75
#define ROBOT_CENTER_TO_BACK    45.8
#define ROBOT_CENTER_TO_FRONT   (ROBOT_LENGTH - ROBOT_CENTER_TO_BACK) // 55.3

#define ROBOT_HALF_LENGTH_FRONT ROBOT_CENTER_TO_FRONT
#define ROBOT_HALF_LENGTH_REAR  ROBOT_CENTER_TO_BACK

/** Robot encoders and wheels */

/** Distance between encoders weels, decrease track to decrease angle */
#define EXT_TRACK_MM      70.0
#define VIRTUAL_TRACK_MM  EXT_TRACK_MM

/* Distance conversion factor. Increase it to go further */

/*  It is a 1024 imps 		--> 4096 because we see 1/4 period
   	Wheel diameter: 25.5mm 	--> perimeter 80.11mm
   	Distance coeficient 	--> 4096/88.11 = 51,129 imps/mm 
 */
#define IMP_ENCODERS 		1024.0
#define WHEEL_DIAMETER_MM 	25.5 // XXX: Rear wheels. Maybe 25.55 or 25.6 is OK
#define WHEEL_PERIM_MM 	    (WHEEL_DIAMETER_MM * M_PI)
#define IMP_COEF 			10.0
#define DIST_IMP_MM 		(((IMP_ENCODERS*4) / WHEEL_PERIM_MM) * IMP_COEF)

/** End of robot parameters ***************************************************/

/** Scheduler events priorities and periods */

/* XXX: These are the initial events, but tthers SW modules may add more 
		events on demand, like the trajectory manager
 */

#define EVENT_PRIORITY_BATTERY 170
#define EVENT_PRIORITY_TIME    160
#define EVENT_PRIORITY_CS      150

#define EVENT_PERIOD_BATTERY 	1000000L
#define EVENT_PERIOD_TIME		TIME_PRECISION
#define EVENT_PERIOD_CS 		1000L


/* Control system block structure */
struct cs_block {
	uint8_t on;
	struct cs cs;
  	struct pid_filter pid;
	struct quadramp_filter qr;
	struct blocking_detection bd;
};

/* General data structure */
struct genboard
{
	/* Command line interface */
	struct rdline rdl;
	char prompt[RDLINE_PROMPT_SIZE];

	/* Encoders */
	#define ENCODER_LEFT  ((void*)2)
	#define ENCODER_RIGHT ((void*)1)

	/* Motors */
	#define MOTOR_LEFT    ((void*)2)
	#define MOTOR_RIGHT   ((void*)1)

	/* Logging and debug */
	#define E_USER_STRAT        194
	#define E_USER_SENSOR       196
	#define E_USER_CS           197

	#define NB_LOGS 10
	uint8_t logs[NB_LOGS+1];
	uint8_t log_level;
	uint8_t debug;
};

/* Robot data structure */
struct mainboard
{
	/* Events flags */
#define DO_ENCODERS   1
#define DO_CS         2
#define DO_RS         4
#define DO_POS        8
#define DO_BD         16
#define DO_TIMER      32
#define DO_POWER      64
#define DO_TM_DATA	  128
	uint16_t flags;

	/* Control systems */
	struct cs_block angle;
	struct cs_block distance;

	/* Robot system */
	struct robot_system rs;

	/* Robot position */
	struct robot_position pos;

	/* Robot trajectories */
  	struct trajectory traj;

	/* Current speeds */
	volatile int16_t speed_a;
	volatile int16_t speed_d;

	/* Current motors PWM */
	int32_t motor_pwm_left;
	int32_t motor_pwm_right;

};

extern struct genboard gen;
extern struct mainboard mainboard;

/* Useful macro for wait a condition or a timeout */
#define WAIT_COND_OR_TIMEOUT(cond, timeout)                   \
({                                                            \
        microseconds __us = time_get_us2();                   \
        uint8_t __ret = 1;                                    \
        while(! (cond)) {                                     \
                if (time_get_us2() - __us > (timeout)*1000L) {\
                        __ret = 0;                            \
                        break;                                \
                }                                             \
        }                                                     \
	if (__ret)					      \
		DEBUG(E_USER_STRAT, "cond is true at line %d",\
		      __LINE__);			      \
	else						      \
		DEBUG(E_USER_STRAT, "timeout at line %d",     \
		      __LINE__);			      \
							      \
        __ret;                                                \
})
#endif

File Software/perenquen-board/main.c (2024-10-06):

/*
 *  Copyright Javier Baliñas Santos (2024)
 *
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
 *  Revision : $Id$
 *
 *  Javier Baliñas Santos <balinas@gmail.com>
 */

#include <stdio.h>
#include <string.h>

#include <aversive.h>
#include <aversive/pgmspace.h>
#include <aversive/wait.h>
#include <aversive/error.h>

#ifndef HOST_VERSION
#include <configuration_bits_config.h>
#endif

#include <uart.h>
#include <encoders_dspic.h>
#include <scheduler.h>
#include <clock_time.h>
#include <pid.h>
#include <quadramp.h>
#include <control_system_manager.h>
#include <trajectory_manager.h>

#include <vect_base.h>
#include <lines.h>
#include <polygon.h>

#include <blocking_detection_manager.h>
#include <robot_system.h>
#include <position_manager.h>

#include <parse.h>
#include <rdline.h>

#include <oscillator.h>

#include "main.h"
#include "strat.h"
#include "cmdline.h"
#include "sensor.h"
#include "actuator.h"
#include "cs.h"

#include "robotsim.h"
#include "strat_base.h"

#include "telemetry.h"
#include "hc05.h"
#include "battery.h"
#include "mcu_setup.h"
#include "leds.h"

struct genboard gen;
struct mainboard mainboard;


int main(void)
{
	/* Disable interrupts */
	cli();

#ifndef HOST_VERSION
	/* Board pins setup */
	io_setup();

	/* Brake motors */
	BRAKE_ON();

	/* Oscillator setup */
	oscillator_init();

	/* Turn off LEDs */
	LED1_OFF();
	LED2_OFF();
	LED3_OFF();
	LED4_OFF();
#endif /* HOST_VERSION */

	/* Clear data structures */
	memset(&gen, 0, sizeof(gen));
	memset(&mainboard, 0, sizeof(mainboard));

	/* Init task flags */
    mainboard.flags = DO_ENCODERS | DO_RS | DO_POS | DO_POWER; // | DO_CS | DO_BD;

#ifndef HOST_VERSION
	/* UART setup */
	uart_init();
	
	#ifdef CONFIG_HC05_SETUP
	/* Bluetooth setup. Never returns */
	hc05_setup();
	#endif

	/* Emergency reset mechanism. Reset is done if "pop" string is received */
	uart_register_rx_event(CMDLINE_UART, emergency);
#endif /* HOST_VERSION */

	/* Register logging functions */
	error_register_emerg(mylog);
	error_register_error(mylog);
	error_register_warning(mylog);
	error_register_notice(mylog);
	error_register_debug(mylog);

#ifndef HOST_VERSION
	/* Encoders setup */
	encoders_dspic_init();

	/* Motors PWM setup */
	hspwm_init();
	hspwm_set_pwm(MOTOR_LEFT, 0);
	hspwm_set_pwm(MOTOR_RIGHT, 0);

	/* Main timer setup */
	timer1_setup();

#endif /* HOST_VERSION */

	/* Scheduler setup */
	scheduler_init();

#ifdef HOST_VERSION
	/* Host simulation setup */
	hostsim_init();
	robotsim_init();
#endif

	/* Time setup. It register a scheduler task */
	time_init(EVENT_PRIORITY_TIME);

	/* Robot control systems setup (distance, angle, ...) */
	maindspic_cs_init();

	/* Robot sensors setup */
	sensor_init();

	/* Battery event */
#ifndef HOST_VERSION
	scheduler_add_periodical_event_priority(do_battery_check, NULL,
		EVENT_PERIOD_BATTERY / SCHEDULER_UNIT, EVENT_PRIORITY_BATTERY);
#endif

	/* Logging setup */
 	gen.logs[0] = E_USER_STRAT;
 	gen.log_level = 5;

	/* Enable interrupts */
	sei();

	/* Say hello */
	printf("\r\n\r\n");
	printf("Hi there!! I'm Perenquen Robot :) \r\n");
	printf("\r\n");
	printf("Battery voltage: %d mV\n\r", sensor_get_battery_mv());
	printf("\r\n");

	/* Init telemetry */
	tm_data_init();

	/* Process commands, never returns */
	cmdline_interact();

	return 0;
}

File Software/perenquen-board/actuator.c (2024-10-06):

/*
 *  Copyright Javier Baliñas Santos (2018)
 *
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
 *  Revision : $Id$
 *
 *  Javier Baliñas Santos <balinas@gmail.com>
 */

#include <aversive.h>
#include <encoders_dspic.h>



#include "actuator.h"
#include "main.h"
#include "robotsim.h"

#ifndef HOST_VERSION
void hspwm_init(void)
{
	/* Use PWM generators 1 and 2.
		 H-bridge control type: unipolar-2Q (PWM only on half-bridge at time)
	 */

	/* Set PWM Period on Primary Time Base */
	/*
		PTPER, PHASEx, SPHASEx = FOSC / (FPWM * PWM_Input_Clock_Prescaler)
		Bit resolution = log2(PTPER)

		FPWM = desired frequency
		FOSC = Oscillator outpur (120MHz for 60 MIPS)
		PWM_Input_Clock_Prescaler = value of PCLKDIV (PTCON2 reg.)

		PTPER = 120MHZ / (20kHz x 1) = 6000

		FPWM = 20kHz
		FOSC = 120MHz
		PWM_Input_Clock_Prescaler = 1:1
	*/
	PTPER = 6000;

	/* Set Phase Shift */
	PHASE1 	= 0;
	SPHASE1 = 0;
	PHASE2 	= 0;
	SPHASE2 = 0;

	/* Set Duty Cycles */
	PDC1 = 0;
	SDC1 = 0;
	PDC2 = 0;
	SDC2 = 0;

	/* Set Dead Time Values */
	DTR1 = DTR2 = 0;
	ALTDTR1 = ALTDTR2 = 0;

	/* Set PWM Mode to Independant and polarity inverted */
	IOCON1 = IOCON2 = 0xFC00;

	/* Set Primary Time Base, Edge-Aligned Mode and Independent Duty Cycles */
	PWMCON1 = PWMCON2 = 0x0000;

	/* Configure Faults (disabled) */
	FCLCON1 = FCLCON2 = 0x0003;

	/* 1:1 Prescaler */
	PTCON2 = 0x0000;

	/* Enable PWM Module */
	PTCON = 0x8000;
}

void hspwm_set_pwm(void* gen_num, int16_t val) {

	#define DUTY_MAX 6000

	switch ((int)gen_num) {
		case 1:
			/* XXX: same sign for both motors */
			if (val >= 0) {	SDC1 = val;	PDC1 = 0; }
			else 					{ SDC1 = 0; 	PDC1 = -val; 	}
			break;

		case 2:
			if (val >= 0) {	SDC2 = val; PDC2 = 0;	}
			else 					{ SDC2 = 0; 	PDC2 = -val; 	}
      break;

		default:
			break;
	}
}
#endif /* !HOST_VERSION */

void motor_pwm_set_and_save(void *pwm_gen_num, int32_t val)
{
#define MOTOR_RIGHT_OFFSET	0
#define MOTOR_LEFT_OFFSET   0

#define MOTOR_RIGHT_MAX		(HSPWM_DUTY_MAX-MOTOR_LEFT_OFFSET)
#define MOTOR_LEFT_MAX		(HSPWM_DUTY_MAX-MOTOR_RIGHT_OFFSET)

	if (pwm_gen_num == MOTOR_LEFT)
	{
		/* Do the saturation here, before saving the value */
		if (val > MOTOR_LEFT_MAX)
			val = MOTOR_LEFT_MAX;
		if (val < -MOTOR_LEFT_MAX)
			val = -MOTOR_LEFT_MAX;

		/* Save value */
		mainboard.motor_pwm_left = val;
	}
	else if (pwm_gen_num == MOTOR_RIGHT)
	{
		/* Do the saturation here, before saving the value */
		if (val > MOTOR_RIGHT_MAX)
			val = MOTOR_RIGHT_MAX;
		if (val < -MOTOR_RIGHT_MAX)
			val = -MOTOR_RIGHT_MAX;

		/* Save value */
		mainboard.motor_pwm_right = val;
	}

	/* Set value */
#ifdef HOST_VERSION
	robotsim_pwm(pwm_gen_num, val);
#else
	hspwm_set_pwm(pwm_gen_num, val);
#endif
}

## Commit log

2017-10-14 Some design notes and almost the mechanic design done
    [AS5000_MD6H_1.fcstd, C-SFL682ZZ.stp, F682ZZ.fcstd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]
2017-10-17 Some improvements on gearbox support
    [gearbox_support_rigth.fcstd]
2017-10-22 Added screw and nut holes to the main support. Created motor assembly with PCB pins
    [gearbox_support_rigth.fcstd, mmgm-carbon-assembly.fcstd, pin-pcb.fcstd]
2017-10-24 Added preliminary perenquen-board
    [perenquen.kicad_pcb, perenquen.sch]
2017-10-25 Almost all main ICs
    [perenquen.sch]
2017-10-28 [MECH] Created manufacture STL parts. [HW] All ICs included on sch. Some functional blocks done.
    [gearbox_support_left.fcstd, magnent_support.stl, magnet_support.fcstd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]
2017-10-29 Almost ready for PCB layout
    [motor_block.fcstd, motor_block_plant.dxf, motor_block_plant.fcstd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]
2017-11-01 [SCH][BOM] Done. [PCB][FOOTPRINTS] In progress
    [20171101_untitled_bom.csv, motor-block_plant2.fcstd, motor_block_plant.dxf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]
2017-11-02 Almos ready for PCB layout. Some footprints error after loadding netlist
    [motor-block_plant2.fcstd, motor_block_plant2.dxf, motor_block_plant3.dxf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]
2017-11-03 [PCB] Mechanical parts placement done
    [MIN7 PCB template.dxf, motor_block.fcstd, perenquen.kicad_pcb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]
2017-11-04 [PCB] H-bridges done
    [perenquen.kicad_pcb, perenquen.sch]
2017-11-04 [PCB] All parts groups placed and partialy routed
    [perenquen.kicad_pcb]
2017-11-05 [PCB] Design done
    [MIN7 PCB template.dxf, perenquen.kicad_pcb, perenquen.sch]
2017-11-05 [PCB] Generated manufacture files
    [perenquen-B.Cu.gbr, perenquen-F.Cu.gbr, perenquen-NPTH-drl_map.gbr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]
2017-11-05 [PCB] Added edge cuts gerber file
    [perenquen-B.Cu.gbr, perenquen-Edge.Cuts.gbr, perenquen-F.Cu.gbr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]
2017-12-26 Minor changes (I think)
    [perenquen.csv, perenquen.kicad_pcb]
2018-10-04 [MECH] New parts organization. New motor block assembly in progress.
    [AS5000_MD6H_1.fcstd, C-SFL682ZZ.stp, F682ZZ.fcstd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]
2018-10-06 [MECH] First version of gearbox supports recovered from OSWHDem17 branch
    [gearbox_support_left.fcstd, gearbox_support_rigth.fcstd, gearbox_support_v2_left.fcstd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]
2018-10-07 [MECH] Assemblies has been updated. Added robot assemby and perequen boards 3d models
    [encoderboard_rigth.fcstd, gearbox_support_left.fcstd, gearbox_support_rigth.fcstd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]
2018-10-07 Uncommited minor changes
    [gearbox_support_left.fcstd, gearbox_support_rigth.fcstd]
2018-11-03 [SW] Added source code from P.Tinto robot.
    [configuration_bits_config.h]
2018-11-04 [FW] Removed NA code, firts compilation. [FW][ENCODERS] Right is workinkg, left seems to have a pin contact issue.
    [configuration_bits_config.h]
2018-11-04 [FW] HW validation done. All HW is working, even the gyro :-). It's been necesary to solder some vias/pads again and change the gain of one diagonal sensors. Take with care, if robot crash don't trus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
    [main.c, main.h]
2018-11-04 [SW] HS PWM module driver done and working. Motor PWM test command updated with new driver.
2018-11-04 [SW] Set physical dimension stuff.
    [perenquen.kicad_pcb]
2018-11-06 [SW] Sensors aquisition in progress....
2018-11-08 [SW] Sensors working
2018-11-10 [SW] Turn bub fixed
    [commands_mainboard.c]
2018-11-19 [SW] FIX wall tracker bug
    [commands_mainboard.c]
2019-04-09 [PYTHON][CMD] Tune command improvements [CMDLINE] Added echo command, goto telemetry improvements. [FIX][CMD] Sensors show bug [CS] Period now is 1ms, added pin debug traces. New cs debug function. [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
    [cmdline.c, commands.c, commands_gen.c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]
2019-04-14 [PYTHON][CMD] Added support for RFCOMM connection directly instead of pass thru serial. [TELEMETRY][FIXME] 1ms data rate not supported by HC-05. Tests with UART cable works perfectly.
    [cmdline.c, commands_mainboard.c, commands_traj.c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]
2019-11-03 Added BOM used in PCBA. Kicad project migrated to Kicad 5.99.
    [perenquen.kicad_pcb, perenquen_bom_pcba.ods]
2019-11-03 Updated design notes.
    [design_notes.ods]
2019-11-03 [FW] Battery monitoring moved to ledd toggle event. [FW] Left motor driver go away. Motor PWM set commented (PWM disabled). [FW] Added some data telemetry test code.
2019-11-03 Minor changes
    [motor_block_plant3.dxf]
2019-11-03 [HW][FIX] Motor was burned [FW][TELEMETRY] Period set to 3ms (3xTs) [FW] PWM is set to 0 if low battery
    [design_notes.ods]
2019-11-03 [FW] BT is disabled if low battery. [FW][TODO] Detect low battery with several samples.
2019-11-05 PWM polarity inverved
2019-11-07 Low battery threshold set to 5 seconds. PWM polarity inverted is working. New acc, speed and cs gains (TBT)
    [design_notes.ods]
2019-11-08 [TEST] Works fine with start gain 30.
    [design_notes.ods]
2024-09-29 Got host compilaton, robot simulator and display.
    XXX: Scheduler host does not support 250us period, set to 1ms. Time base set to 10ms.
    FIXME: gound field blocking simulation. Disabled.
    [actuator.c, commands_mainboard.c, display.py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]
2024-10-05 Kicad project updated to v8.0
    [perenquen.kicad_pcb, perenquen.kicad_sch]
2024-10-06 New ADC sensor reading sequence in progress.
2024-10-06 Refactored ADC sensor aquisition. Code review and house keeping.
    - Removed deprecated Eurobot code from main
    - TODO: review strat files
    - Moved LEDS, battery, HC05 and MCU setup functions to specific files
    - Reviewed main files. Spread some main.h code to more convenient files.
2024-10-07 Added LEDs supports. Two types, front and side LEDs
    [leds_front_support.FCStd, leds_side_support.FCStd]
2024-10-07 Added stl files of LEDs supports
    [leds_front_support_1.stl, leds_side_support_1.stl]

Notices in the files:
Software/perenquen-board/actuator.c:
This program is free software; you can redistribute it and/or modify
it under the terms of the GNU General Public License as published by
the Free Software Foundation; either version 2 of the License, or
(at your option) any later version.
